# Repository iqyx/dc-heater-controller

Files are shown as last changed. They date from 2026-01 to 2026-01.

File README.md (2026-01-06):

# 48 V heater controller

This aims to be a home-assistant compatible heater controller for off-grid water heating using
surplus electricity from a PV array. It is intended to be used in a 48 V DC system. Some main features:

- turn on the heating element whenever a surplus energy is detected
- cycle multiple heating elements to wear them evenly
- optimized for "3-phase" 48 V heating elements
- multiple redundant protections
- STM32 MCU with a ST's WiFi module for connectivity (no, no ESP32)
- water pump control

Implemented protections:

- high side MOSFET disconnect on UVLO (prevent draining the battery), can be set using a trimpot on the power board
- high side MOSFET disconnect on OV (well, not really important)
- high side MOSFET hardware overtemperature protection (turns them off)
- high side MOSFET software temperature monitoring
- high side current and voltage sense
- high side and low side MOSFETs software control depending on the battery voltage
- 95° water overtemperature hardware protection (a bimetal thermostat turns off high side MOSFETs)
- 90° water overtemperature hardware protection (a NTC with a comparator turns off low side MOSFETs independently of the software control)
- water temperature setpoint control (software controls low side MOSFETs)
- water pump malfunction turns off low side MOSFETs (software)

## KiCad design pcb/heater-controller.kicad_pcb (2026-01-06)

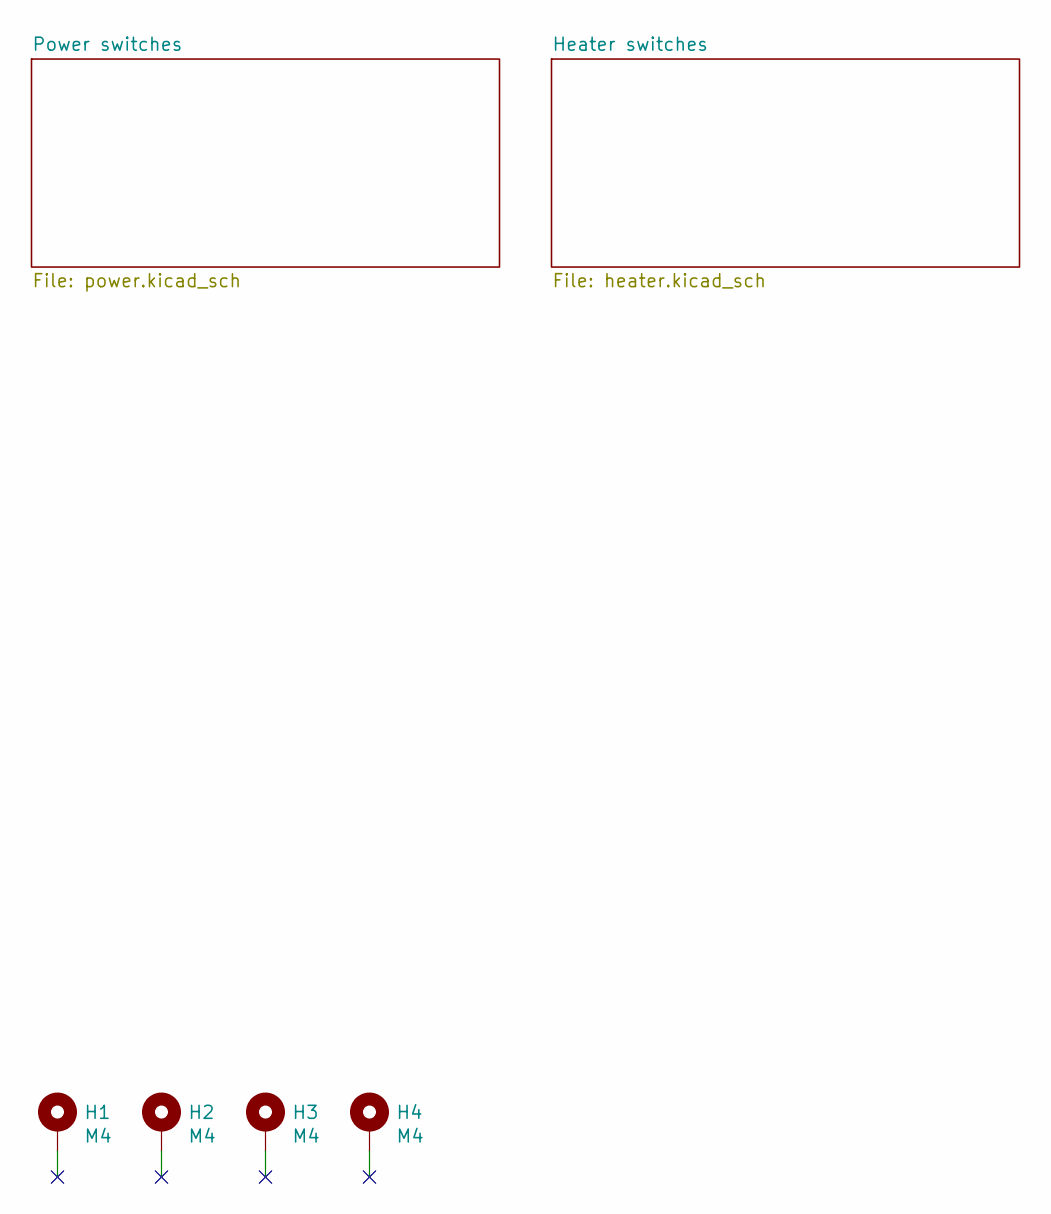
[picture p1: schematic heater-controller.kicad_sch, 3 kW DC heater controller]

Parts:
H1, H2, H3, H4: M4; MountingHole_4.3mm_M4_Pad_Via

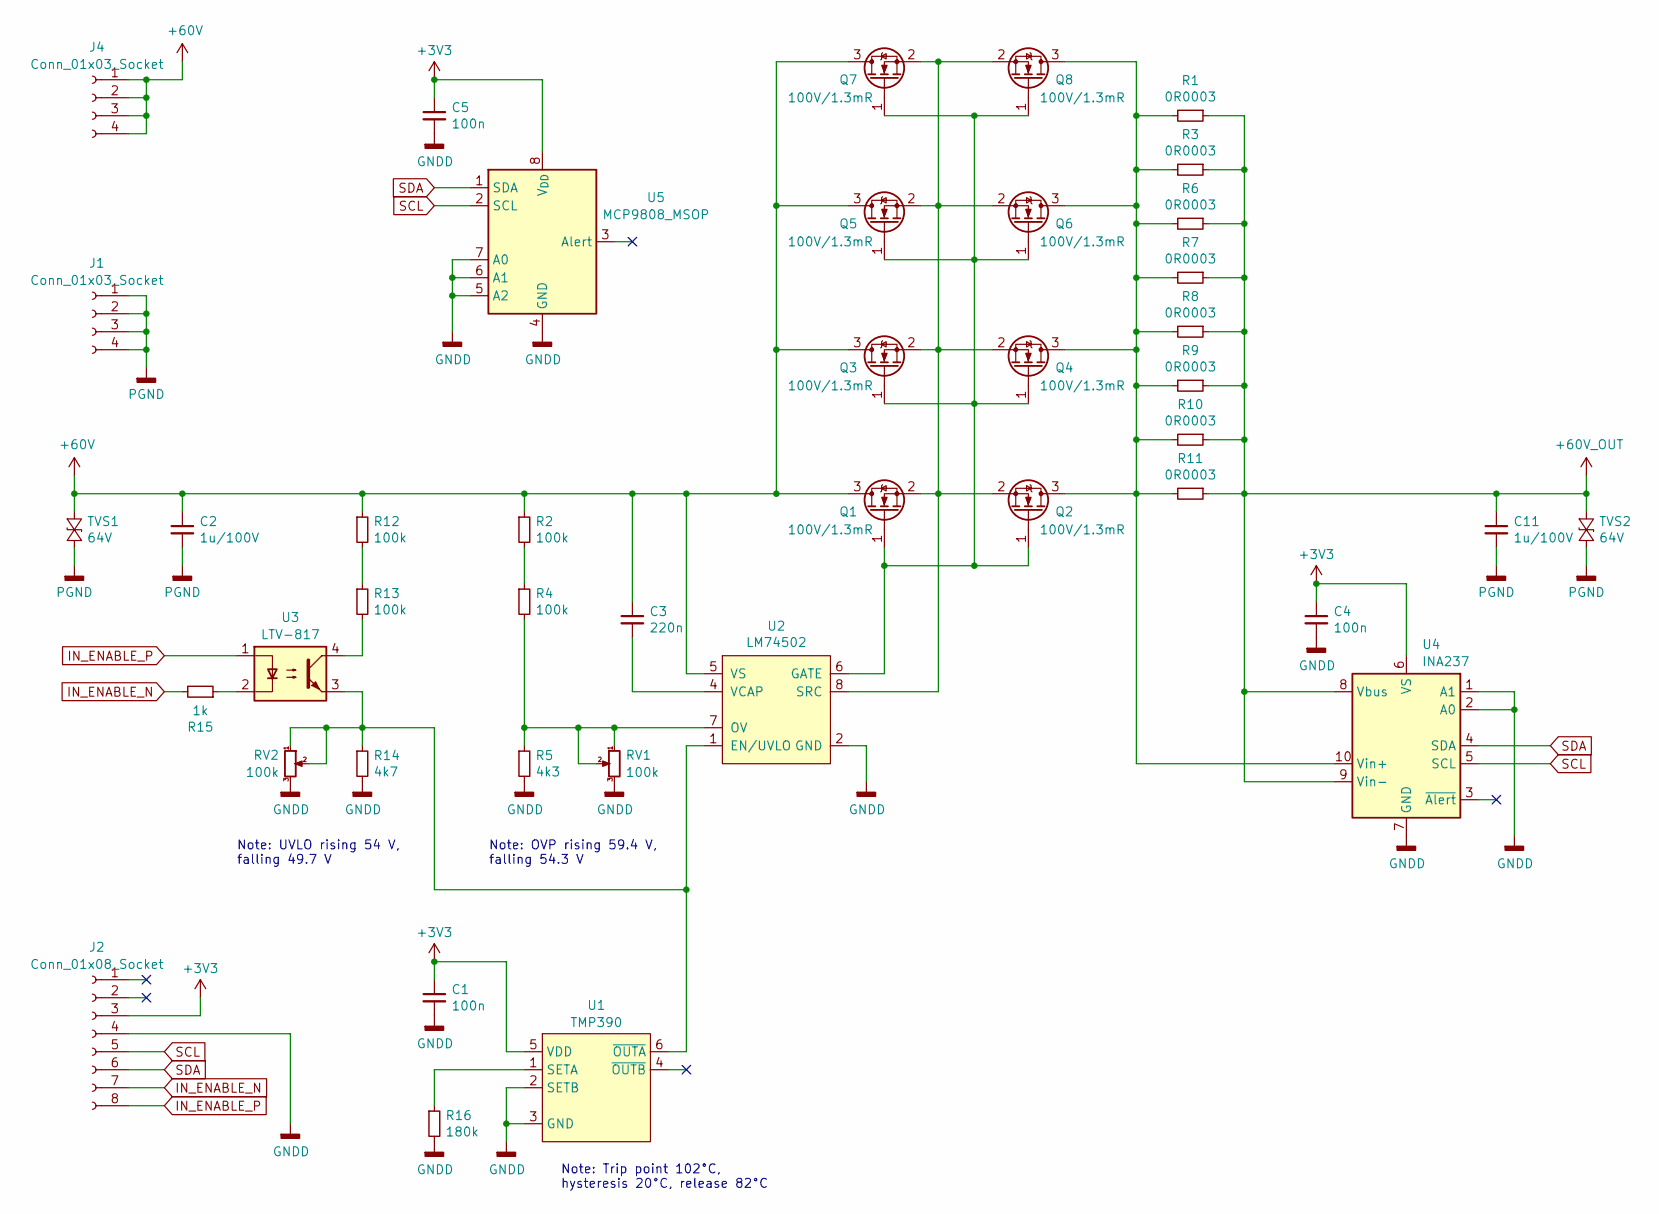
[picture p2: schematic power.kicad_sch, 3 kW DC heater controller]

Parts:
C1, C4, C5: 100n; C_0603_1608Metric
C2, C11: 1u/100V; C_1210_3225Metric
C3: 220n; C_0603_1608Metric
J1, J4: Conn_01x03_Socket; PinHeader_1x04_P2.54mm_Vertical
J2: Conn_01x08_Socket; PinHeader_1x08_P2.54mm_Vertical
Q1, Q2, Q3, Q4, Q5, Q6, Q7, Q8: 100V/1.3mR; Infineon_PG-HSOF-8-1
R1, R3, R6, R7, R8, R9, R10, R11: 0R0003; R_2512_6332Metric_Pad1.40x3.35mm_HandSolder
R2, R4, R12, R13: 100k; R_0603_1608Metric
R5: 4k3; R_0603_1608Metric
R14: 4k7; R_0603_1608Metric
R15: 1k; R_0603_1608Metric
R16: 180k; R_0603_1608Metric
RV1, RV2: 100k; Potentiometer_Bourns_3296Y_Vertical
TVS1, TVS2: 64V; D_SMC
U1: TMP390; SOT-666
U2: LM74502; SOT-23-8
U3: LTV-817; DIP-4_W7.62mm
U4: INA237; VSSOP-10_3x3mm_P0.5mm
U5: MCP9808_MSOP; MSOP-8_3x3mm_P0.65mm

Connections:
+3V3: C1.1, C4.1, C5.1, J2.3, U1.5 (VDD), U4.6 (VS), U5.8 (V_{DD})
+60V: C2.1, C3.1, J4.1, J4.2, J4.3, J4.4, Q1.3 (D), Q3.3 (D), Q5.3 (D), Q7.3 (D), R2.1, R12.1, TVS1.1 (K), U2.5 (VS)
+60V_OUT: C11.1, R1.1, R3.1, R6.1, R7.1, R8.1, R9.1, R10.1, R11.1, TVS2.1 (K), U4.8 (Vbus), U4.9 (Vin-)
GNDD: C1.2, C4.2, C5.2, J2.4, R5.2, R14.2, R16.2, RV1.3, RV2.3, U1.2 (SETB), U1.3 (GND), U2.2 (GND), U4.1 (A1), U4.2 (A0), U4.7 (GND), U5.4 (GND), U5.5 (A2), U5.6 (A1), U5.7 (A0)
IN_ENABLE_N: J2.7, R15.2
IN_ENABLE_P: J2.8, U3.1
unnamed: Q1.1 (G), Q2.1 (G), Q3.1 (G), Q4.1 (G), Q5.1 (G), Q6.1 (G), Q7.1 (G), Q8.1 (G), U2.6 (GATE)
unnamed: Q1.2 (S), Q2.2 (S), Q3.2 (S), Q4.2 (S), Q5.2 (S), Q6.2 (S), Q7.2 (S), Q8.2 (S), U2.8 (SRC)
unnamed: Q2.3 (D), Q4.3 (D), Q6.3 (D), Q8.3 (D), R1.2, R3.2, R6.2, R7.2, R8.2, R9.2, R10.2, R11.2, U4.10 (Vin+)
unnamed: R2.2, R4.1
unnamed: R12.2, R13.1
unnamed: R13.2, U3.4
unnamed: R15.1, U3.2
unnamed: R16.1, U1.1 (SETA)
unnamed: R14.1, RV2.1, RV2.2, U1.6 (~OUTA), U2.1 (EN/UVLO), U3.3
unnamed: R4.2, R5.1, RV1.1, RV1.2, U2.7 (OV)
unnamed: C3.2, U2.4 (VCAP)
PGND: C2.2, C11.2, J1.1, J1.2, J1.3, J1.4, TVS1.2 (A), TVS2.2 (A); also elsewhere on the board
SCL: J2.5, U4.5 (SCL), U5.2 (SCL)
SDA: J2.6, U4.4 (SDA), U5.1 (SDA)

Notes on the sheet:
Note: Trip point 102°C, hysteresis 20°C, release 82°C
Note: OVP rising 59.4 V, falling 54.3 V
Note: UVLO rising 54 V, falling 49.7 V

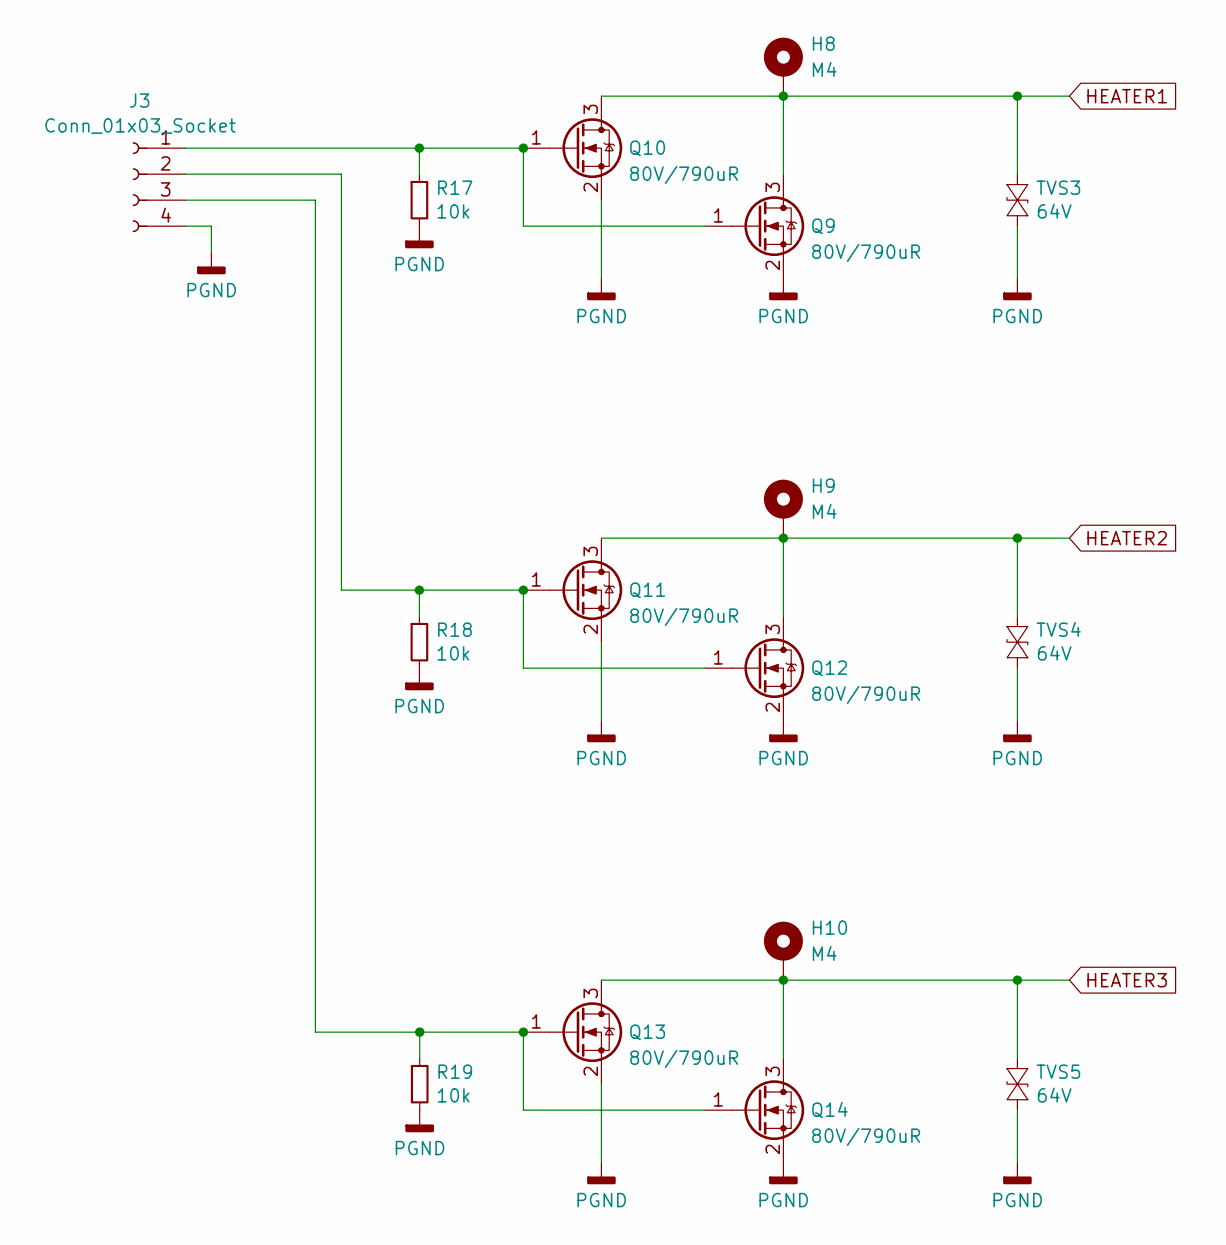
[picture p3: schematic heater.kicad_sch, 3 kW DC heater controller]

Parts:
H8, H9, H10: M4; KEYS_7798
J3: Conn_01x03_Socket; PinHeader_1x04_P2.54mm_Vertical
Q9, Q10, Q11, Q12, Q13, Q14: 80V/790uR; Infineon_PG-HSOF-8-1
R17, R18, R19: 10k; R_0603_1608Metric
TVS3, TVS4, TVS5: 64V; D_SMC

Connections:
HEATER1: H8.1, Q9.3 (D), Q10.3 (D), TVS3.1 (K)
HEATER2: H9.1, Q11.3 (D), Q12.3 (D), TVS4.1 (K)
HEATER3: H10.1, Q13.3 (D), Q14.3 (D), TVS5.1 (K)
unnamed: J3.1, Q9.1 (G), Q10.1 (G), R17.1
unnamed: J3.2, Q11.1 (G), Q12.1 (G), R18.1
unnamed: J3.3, Q13.1 (G), Q14.1 (G), R19.1
PGND: J3.4, Q9.2 (S), Q10.2 (S), Q11.2 (S), Q12.2 (S), Q13.2 (S), Q14.2 (S), R17.2, R18.2, R19.2, TVS3.2 (A), TVS4.2 (A), TVS5.2 (A); also elsewhere on the board

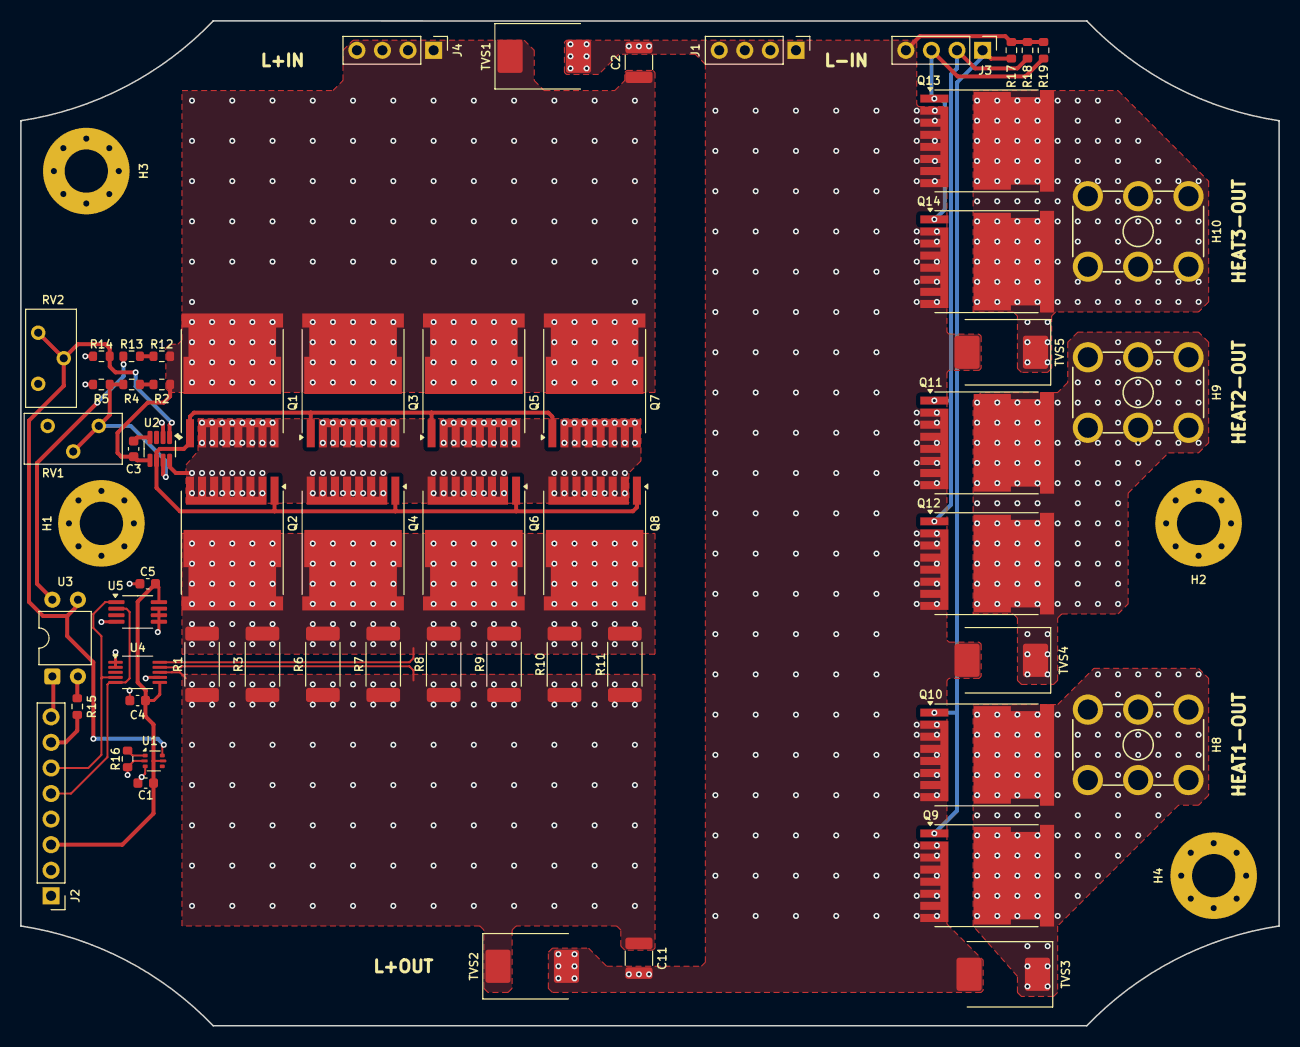
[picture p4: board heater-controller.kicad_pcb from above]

Board: 2 copper layers, 125.0 x 99.8 mm, 62 parts (0 on the bottom side), 26 nets.

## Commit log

2026-01-06 Update sch & pcb
    [heater-controller.kicad_pcb, heater-controller.kicad_sch, heater.kicad_sch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]
2026-01-06 chore: Add gerber output

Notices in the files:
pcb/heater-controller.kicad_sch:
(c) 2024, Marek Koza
